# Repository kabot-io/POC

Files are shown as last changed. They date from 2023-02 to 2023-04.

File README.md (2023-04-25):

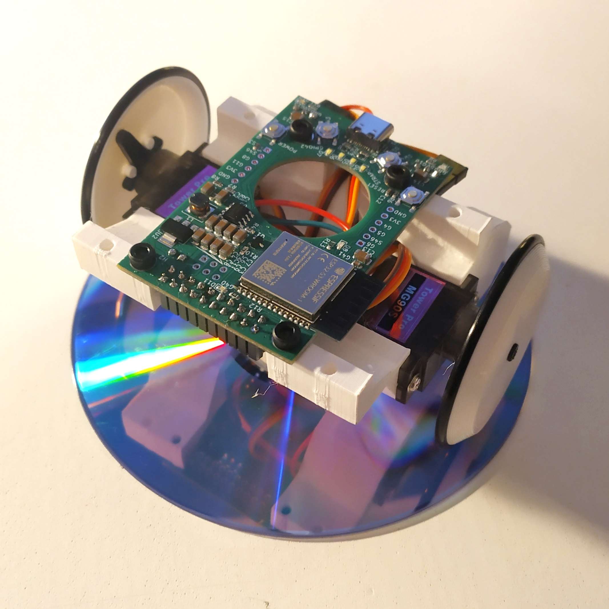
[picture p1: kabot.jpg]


# Kabot - lowering entry barrier to ROS2

The Kabot robot is a hardware and software solution that lowers the entry barrier to Robot Operating System 2 (ROS2) and provides an expandable platform for makers, students and educators. One of the main obstacles in the adoption of ROS2 by beginners is the high knowledge barrier needed to setup and start tinkering - Kabot mission is to bring batteries included in a box. Think of using Arduino instead of setting up whole toolchain and build system.

The robot is a simple differential drive robot with expansion port for connecting external sensors and actuators, and instead of classic internal odometry sensors uses external camera to track itself in the world. Main goals are to create as simple (thus cost effective) hardware, move as much of heavy lifting as possible to the host PC instead of the robot itself and provide user with simple software environment.

## Hardware
All of the structural parts are designed for FDM printing. Wheels, base, cell holder - PLA will do. For the tires, standard O-Ring seals are used, as they are easily available for a cost next to nothing.

Kabot has two actuators - MG90S servos in a continous rotation version. This way, no on-board H-Bridge is needed, just one GPIO per motor and 5V power. Those servos also come with horns that can be used to attach wheels securely. 

All the electrons needed to keep the robot running are supplied via single 18650 Li-Ion cell. Charging, battery protection, and switching on and off is provided via IPS5306 - chinesium powerbank IC. Power for the charger is supplied via USB-C connector. This converter provides 5V for the servos and expansion port, and LDO provides 3.3V for the SoC and expansion port.

The main board is based around ESP32-S3 chip, sporting 16MB of flash and 8MB of RAM. Why ESP32-S3 instead of base ESP32? S3 has built-in USB peripheral, that hosts USB-JTAG and USB-CDC out of the box, so flashing, GDB and Serial.println() works without any external hardware. Furthermore, S3 is a little beefier, and has reconfigurable GPIO matrix, which will ease development of add-on boards. Most of the communication and other internal peripherals can be configured to use any pin of the package. 

## Installation

To run the robots, you need to install ROS2 Foxy. ROS2 is a software framework designed for robotic systems development. It provides a set of libraries and tools to help developers create robust and complex robot applications.

To install ROS2 Foxy, please follow the instructions provided on the official ROS2 website: [ROS2 Foxy installation](https://docs.ros.org/en/foxy/Installation.html)

## How to launch
To launch the package, you need to run the following command:
```
ros2 launch kabot_launcher kabot.launch.py
```

This will launch the package and start the necessary nodes and processes. If you encounter any issues while launching the package, please make sure to check whether you have all the required dependent packages. You can use the ROS2 package manager (rosdep) to automatically install all required dependencies.

## License

[Hardware: Creative Commons Attribution-NonCommercial-ShareAlike 4.0 International License](https://github.com/kabot-io/POC/blob/main/hardware/LICENSE)

[Software: Apache License, Version 2.0](https://github.com/kabot-io/POC/blob/main/src/LICENSE)

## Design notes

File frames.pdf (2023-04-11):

view_frames Result

world

camera

Broadcaster: default_authority Average rate: 10000.0
Buffer length: 0.0
Most recent transform: 0.0 Oldest transform: 0.0

Recorded at time: 1680135584.4556208

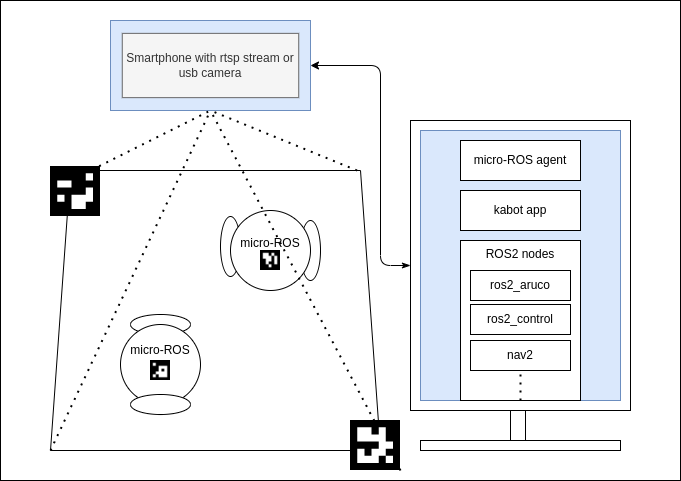
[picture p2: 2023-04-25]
kabot.drawio.png

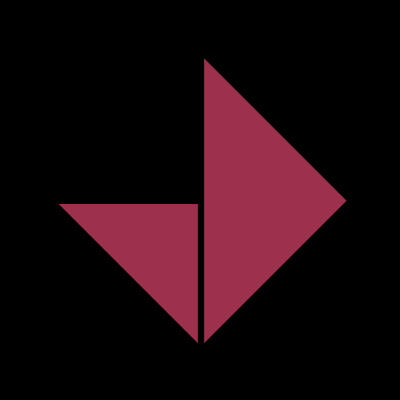
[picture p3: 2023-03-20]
src/kabot_app/src/images/kabot.png

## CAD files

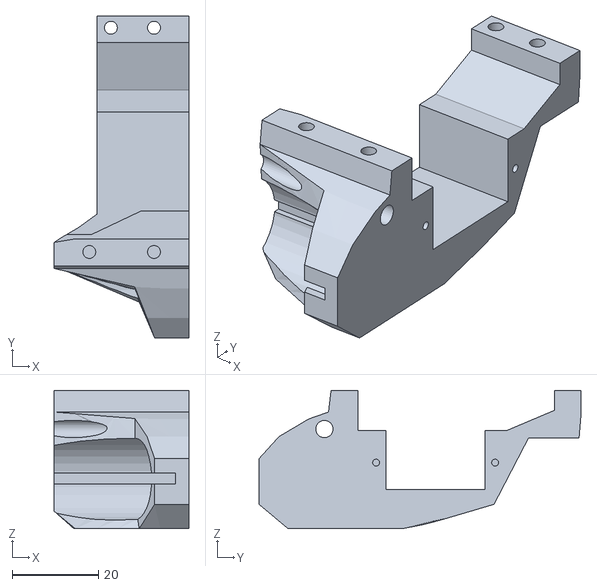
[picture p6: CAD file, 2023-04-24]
hardware/mechanics/printed parts/chassis_right.stl
31.3 x 74.7 x 32.1

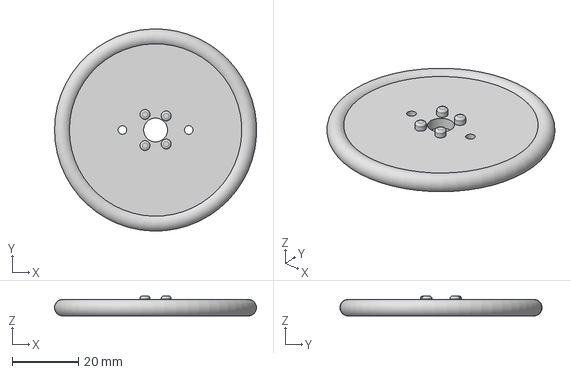
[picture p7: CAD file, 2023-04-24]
hardware/mechanics/printed parts/wheel_v1.step
60.9 x 61.0 x 6.00 mm

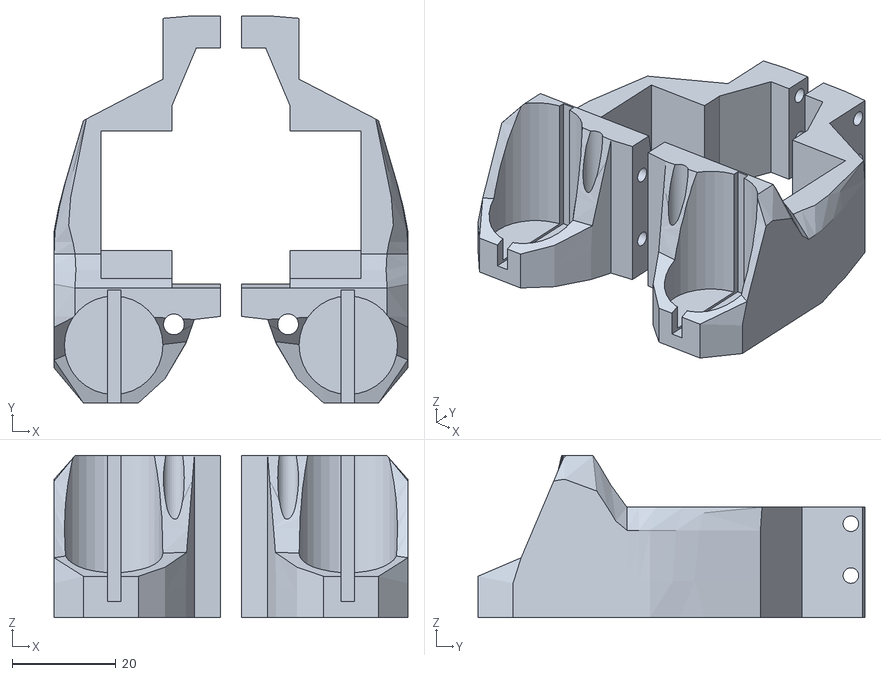
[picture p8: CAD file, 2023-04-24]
hardware/mechanics/printed parts/chassis_both.stl
68.2 x 74.7 x 31.3

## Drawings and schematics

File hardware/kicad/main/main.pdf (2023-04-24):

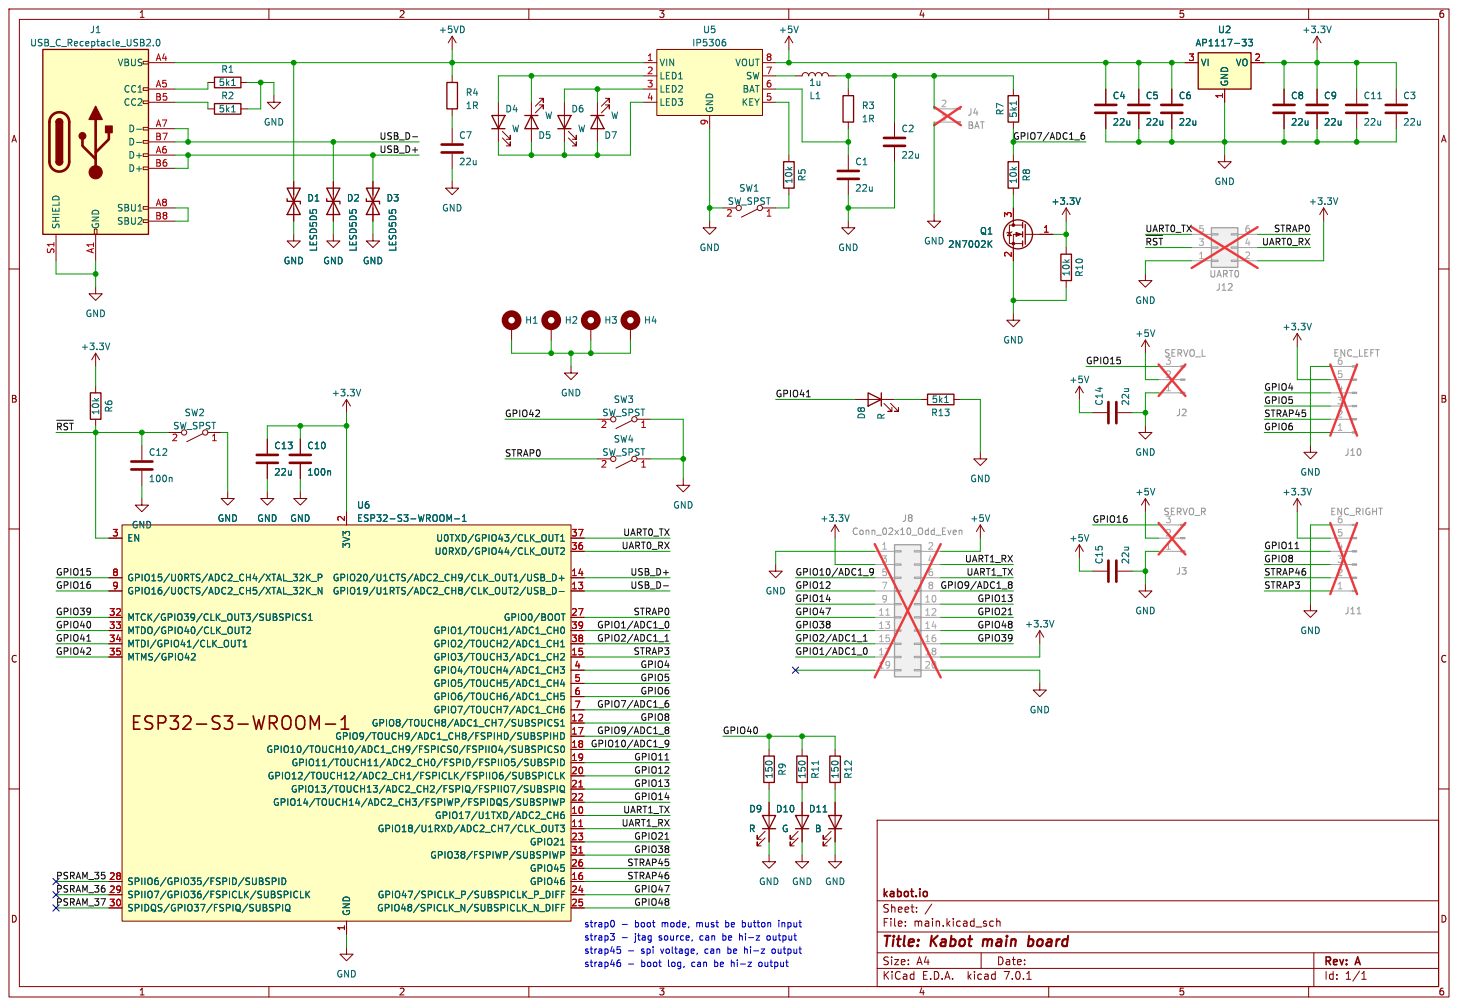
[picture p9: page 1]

2 GPIO12/TOUCH12/ADC2_CH1/FSPICLK/FSPIIO6/SUBSPICLK 20 GPIO13/TOUCH13/ADC2_CH2/FSPIQ/FSPIIO7/SUBSPIQ 21 GPIO14/TOUCH14/ADC2_CH3/FSPIWP/FSPIDQS/SUBSPIWP 22 GPIO21 23 GPIO47/SPICLK_P/SUBSPICLK_P_DIFF 24 GPIO48/SPICLK_N/SUBSPICLK_N_DIFF 25 GPIO45 26 GPIO0/BOOT 27 SPIIO6/GPIO35/FSPID/SUBSPID 28 SPIIO7/GPIO36/FSPICLK/SUBSPICLK 29 EN 3 SPIDQS/GPIO37/FSPIQ/SUBSPIQ 30 GPIO38/FSPIWP/SUBSPIWP 31 MTCK/GPIO39/CLK_OUT3/SUBSPICS1 32 MTDO/GPIO40/CLK_OUT2 33 MTDI/GPIO41/CLK_OUT1 34 MTMS/GPIO42 35 U0RXD/GPIO44/CLK_OUT2 36 U0TXD/GPIO43/CLK_OUT1 37 GPIO2/TOUCH2/ADC1_CH1 38 GPIO1/TOUCH1/ADC1_CH0 39 GPIO4/TOUCH4/ADC1_CH3 4 GPIO5/TOUCH5/ADC1_CH4 5 GPIO6/TOUCH6/ADC1_CH5 6 GPIO7/TOUCH7/ADC1_CH6 7 GPIO15/U0RTS/ADC2_CH4/XTAL_32K_P 8 GPIO16/U0CTS/ADC2_CH5/XTAL_32K_N 9 U6ESP32-S3-WROOM-1 GND

File: main.kicad_sch Sheet: / kabot.io C12

2 GPIO12/TOUCH12/ADC2_CH1/FSPICLK/FSPIIO6/SUBSPICLK 20 GPIO13/TOUCH13/ADC2_CH2/FSPIQ/FSPIIO7/SUBSPIQ 21 GPIO14/TOUCH14/ADC2_CH3/FSPIWP/FSPIDQS/SUBSPIWP 22 GPIO21 23 GPIO47/SPICLK_P/SUBSPICLK_P_DIFF 24 GPIO48/SPICLK_N/SUBSPICLK_N_DIFF 25 GPIO45 26 GPIO0/BOOT 27 SPIIO6/GPIO35/FSPID/SUBSPID 28 SPIIO7/GPIO36/FSPICLK/SUBSPICLK 29 EN 3 SPIDQS/GPIO37/FSPIQ/SUBSPIQ 30 GPIO38/FSPIWP/SUBSPIWP 31 MTCK/GPIO39/CLK_OUT3/SUBSPICS1 32 MTDO/GPIO40/CLK_OUT2 33 MTDI/GPIO41/CLK_OUT1 34 MTMS/GPIO42 35 U0RXD/GPIO44/CLK_OUT2 36 U0TXD/GPIO43/CLK_OUT1 37 GPIO2/TOUCH2/ADC1_CH1 38 GPIO1/TOUCH1/ADC1_CH0 39 GPIO4/TOUCH4/ADC1_CH3 4 GPIO5/TOUCH5/ADC1_CH4 5 GPIO6/TOUCH6/ADC1_CH5 6 GPIO7/TOUCH7/ADC1_CH6 7 GPIO15/U0RTS/ADC2_CH4/XTAL_32K_P 8 GPIO16/U0CTS/ADC2_CH5/XTAL_32K_N 9 D10G
D11B D9 R GND

1 GPIO17/U1TXD/ADC2_CH6 10 GPIO18/U1RXD/ADC2_CH7/CLK_OUT3 11 GPIO8/TOUCH8/ADC1_CH7/SUBSPICS1 12 GPIO19/U1RTS/ADC2_CH8/CLK_OUT2/USB_D- 13 GPIO20/U1CTS/ADC2_CH9/CLK_OUT1/USB_D+ 14 GPIO3/TOUCH3/ADC1_CH2 15 GPIO46 16 GPIO9/TOUCH9/ADC1_CH8/FSPIHD/SUBSPIHD 17 GPIO10/TOUCH10/ADC1_CH9/FSPICS0/FSPIIO4/SUBSPICS0 18 GPIO11/TOUCH11/ADC2_CH0/FSPID/FSPIIO5/SUBSPID 19 3V3

Id: 1/1 Title: Kabot main board

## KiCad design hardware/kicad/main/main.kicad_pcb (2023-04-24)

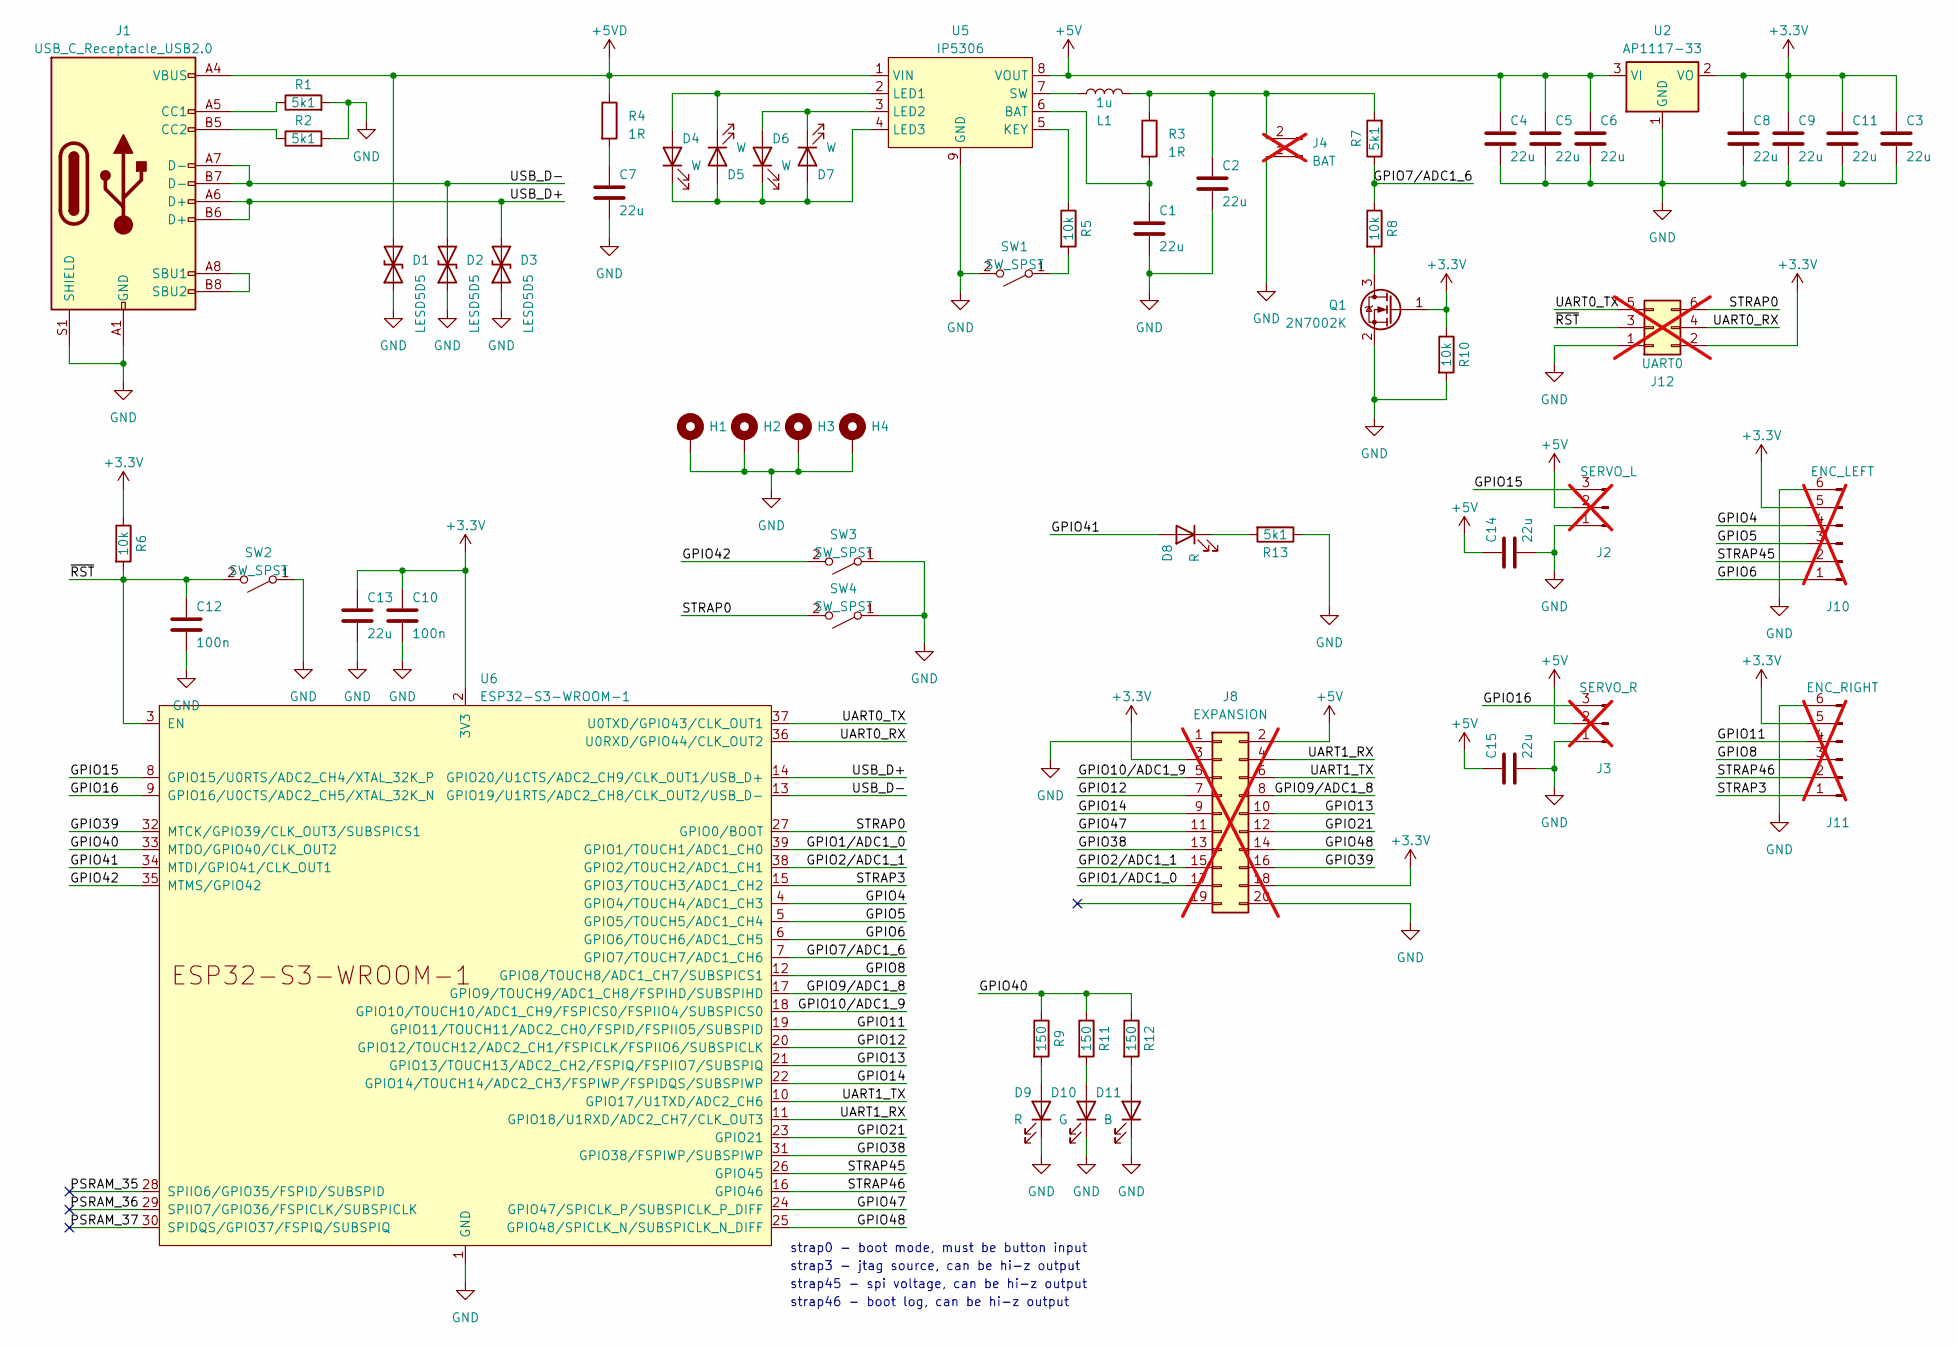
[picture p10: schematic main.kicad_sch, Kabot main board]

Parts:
C1, C2, C3, C4, C5, C6, C7, C8, C9, C11, C13, C14, C15: 22u; C_1206_3216Metric; JLC C12891
C10, C12: 100n; C_0603_1608Metric; JLC C14663
D1, D2, D3: LESD5D5; D_SOD-523; JLC C383211
D4, D5, D6, D7: W; LED_0603_1608Metric; JLC C2290
D8, D9: R; LED_0603_1608Metric; JLC C2286
D10: G; LED_0603_1608Metric; JLC C72043
D11: B; LED_0603_1608Metric; JLC C72041
H1, H2, H3, H4: MountingHole_Pad; MountingHole_3.2mm_M3_DIN965_Pad
J1: USB_C_Receptacle_USB2.0; USB_C_Receptacle_HRO_TYPE-C-31-M-12; JLC C668624
J2: SERVO_L; PinHeader_1x03_P2.54mm_Horizontal; not fitted
J3: SERVO_R; PinHeader_1x03_P2.54mm_Horizontal; not fitted
J4: BAT; PinHeader_1x02_P2.54mm_Horizontal; not fitted
J8: EXPANSION; PinSocket_2x10_P2.54mm_Vertical; JLC C124419; not fitted
J10: ENC_LEFT; PinHeader_1x06_P2.54mm_Horizontal; not fitted
J11: ENC_RIGHT; PinHeader_1x06_P2.54mm_Horizontal; not fitted
J12: UART0; PinHeader_2x03_P2.54mm_Vertical; not fitted
L1: 1u; L_Changjiang_FNR5045S; JLC C436396
Q1: 2N7002K; SOT-23; JLC C8545
R1, R2, R7, R13: 5k1; R_0603_1608Metric; JLC C23186
R3, R4: 1R; R_0603_1608Metric; JLC C22936
R5, R6, R8, R10: 10k; R_0603_1608Metric; JLC C25804
R9, R11, R12: 150; R_0603_1608Metric; JLC C22808
SW1, SW2, SW3, SW4: SW_SPST; SW_SPST_SKQG_WithStem; JLC C318884
U2: AP1117-33; SOT-223-3_TabPin2; JLC C6186
U5: IP5306; Diodes_SO-8EP; JLC C181692
U6: ESP32-S3-WROOM-1; JLC C2913202

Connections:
+3.3V: C3.1, C8.1, C9.1, C10.1, C11.1, C13.1, J8.3, J8.18, J10.5, J11.5, J12.2, Q1.1 (G), R6.1, R10.1, U2.2 (VO), U6.2 (3V3)
+5V: C4.1, C5.1, C6.1, C14.1, C15.1, J2.2, J3.2, J8.2, U2.3 (VI), U5.8 (VOUT)
+5VD: D1.2 (A2), J1.A4 (VBUS), J1.A9 (VBUS), J1.B4 (VBUS), J1.B9 (VBUS), R4.1, U5.1 (VIN)
/GPIO1/ADC1_0: J8.17, U6.39 (GPIO1/TOUCH1/ADC1_CH0)
/GPIO2/ADC1_1: J8.15, U6.38 (GPIO2/TOUCH2/ADC1_CH1)
/GPIO4: J10.4, U6.4 (GPIO4/TOUCH4/ADC1_CH3)
/GPIO5: J10.3, U6.5 (GPIO5/TOUCH5/ADC1_CH4)
/GPIO6: J10.1, U6.6 (GPIO6/TOUCH6/ADC1_CH5)
/GPIO7/ADC1_6: R7.1, R8.1, U6.7 (GPIO7/TOUCH7/ADC1_CH6)
/GPIO8: J11.3, U6.12 (GPIO8/TOUCH8/ADC1_CH7/SUBSPICS1)
/GPIO9/ADC1_8: J8.8, U6.17 (GPIO9/TOUCH9/ADC1_CH8/FSPIHD/SUBSPIHD)
/GPIO10/ADC1_9: J8.5, U6.18 (GPIO10/TOUCH10/ADC1_CH9/FSPICS0/FSPIIO4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)
/GPIO11: J11.4, U6.19 (GPIO11/TOUCH11/ADC2_CH0/FSPID/FSPIIO5/S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)
/GPIO12: J8.7, U6.20 (GPIO12/TOUCH12/ADC2_CH1/FSPICLK/FSPIIO6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)
/GPIO13: J8.10, U6.21 (GPIO13/TOUCH13/ADC2_CH2/FSPIQ/FSPIIO7/S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)
/GPIO14: J8.9, U6.22 (GPIO14/TOUCH14/ADC2_CH3/FSPIWP/FSPIDQS/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)
/GPIO15: J2.3, U6.8 (GPIO15/U0RTS/ADC2_CH4/XTAL_32K_P)
/GPIO16: J3.3, U6.9 (GPIO16/U0CTS/ADC2_CH5/XTAL_32K_N)
/GPIO21: J8.12, U6.23 (GPIO21)
/GPIO38: J8.13, U6.31 (GPIO38/FSPIWP/SUBSPIWP)
/GPIO39: J8.16, U6.32 (MTCK/GPIO39/CLK_OUT3/SUBSPICS1)
/GPIO40: R9.1, R11.1, R12.1, U6.33 (MTDO/GPIO40/CLK_OUT2)
/GPIO41: D8.2 (A), U6.34 (MTDI/GPIO41/CLK_OUT1)
/GPIO42: SW3.2 (B), U6.35 (MTMS/GPIO42)
/GPIO47: J8.11, U6.24 (GPIO47/SPICLK_P/SUBSPICLK_P_DIFF)
/GPIO48: J8.14, U6.25 (GPIO48/SPICLK_N/SUBSPICLK_N_DIFF)
/PSRAM_35: U6.28 (SPIIO6/GPIO35/FSPID/SUBSPID)
/PSRAM_36: U6.29 (SPIIO7/GPIO36/FSPICLK/SUBSPICLK)
/PSRAM_37: U6.30 (SPIDQS/GPIO37/FSPIQ/SUBSPIQ)
/STRAP0: J12.6, SW4.2 (B), U6.27 (GPIO0/BOOT)
/STRAP3: J11.1, U6.15 (GPIO3/TOUCH3/ADC1_CH2)
/STRAP45: J10.2, U6.26 (GPIO45)
/STRAP46: J11.2, U6.16 (GPIO46)
/UART0_RX: J12.4, U6.36 (U0RXD/GPIO44/CLK_OUT2)
/UART0_TX: J12.5, U6.37 (U0TXD/GPIO43/CLK_OUT1)
/UART1_RX: J8.4, U6.11 (GPIO18/U1RXD/ADC2_CH7/CLK_OUT3)
/UART1_TX: J8.6, U6.10 (GPIO17/U1TXD/ADC2_CH6)
/USB_D+: D3.2 (A2), J1.A6 (D+), J1.B6 (D+), U6.14 (GPIO20/U1CTS/ADC2_CH9/CLK_OUT1/USB_D+)
/USB_D-: D2.2 (A2), J1.A7 (D-), J1.B7 (D-), U6.13 (GPIO19/U1RTS/ADC2_CH8/CLK_OUT2/USB_D-)
/~RST: C12.1, J12.3, R6.2, SW2.2 (B), U6.3 (EN)
GND: C1.2, C2.2, C3.2, C4.2, C5.2, C6.2, C7.2, C8.2, C9.2, C10.2, C11.2, C12.2, C13.2, C14.2, C15.2, D1.1 (A1), D2.1 (A1), D3.1 (A1), D9.1 (K), D10.1 (K), D11.1 (K), H1.1, H2.1, H3.1, H4.1, J1.A1 (GND), J1.A12 (GND), J1.B1 (GND), J1.B12 (GND), J1.S1 (SHIELD), J2.1, J3.1, J4.1, J8.1, J8.20, J10.6, J11.6, J12.1, Q1.2 (S), R1.2, R2.2, R10.2, R13.1, SW1.2 (B), SW2.1 (A), SW3.1 (A), SW4.1 (A), U2.1 (GND), U5.9 (GND), U6.1 (GND), U6.40 (GND), U6.41 (GND)
unnamed: C7.1, R4.2
unnamed: D4.2 (A), D5.1 (K), U5.2 (LED1)
unnamed: D4.1 (K), D5.2 (A), D6.1 (K), D7.2 (A), U5.4 (LED3)
unnamed: D6.2 (A), D7.1 (K), U5.3 (LED2)
unnamed: D8.1 (K), R13.2
unnamed: D9.2 (A), R9.2
unnamed: D10.2 (A), R11.2
unnamed: D11.2 (A), R12.2
unnamed: J1.A5 (CC1), R1.1
unnamed: J1.B5 (CC2), R2.1
unnamed: J1.A8 (SBU1), J1.B8 (SBU2)
unnamed: C2.1, J4.2, L1.2, R3.1, R7.2
unnamed: Q1.3 (D), R8.2
unnamed: R5.2, SW1.1 (A)
unnamed: C1.1, R3.2, U5.6 (BAT)
unnamed: R5.1, U5.5 (KEY)
unnamed: L1.1, U5.7 (SW)

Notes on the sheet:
strap3 - jtag source, can be hi-z output
strap45 - spi voltage, can be hi-z output
strap0 - boot mode, must be button input
strap46 - boot log, can be hi-z output

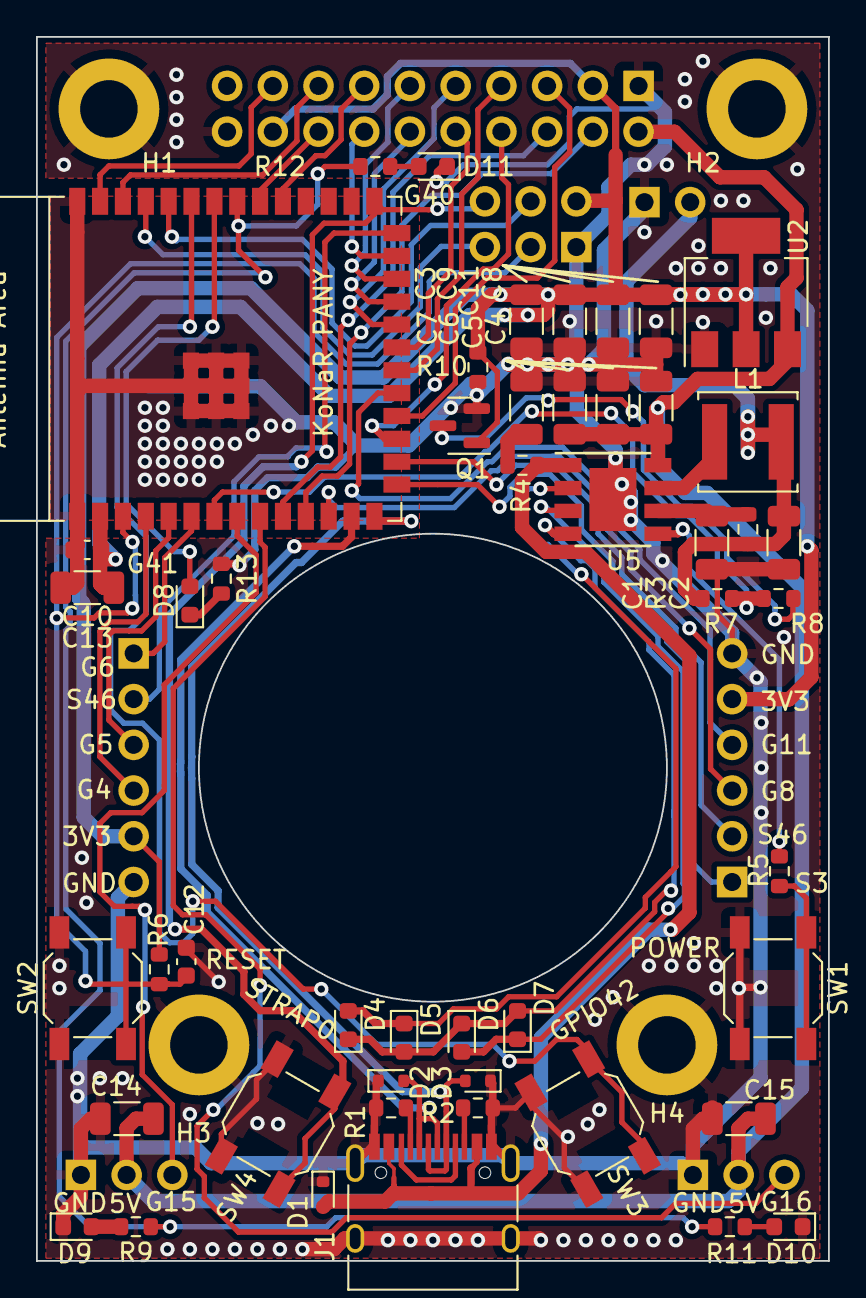
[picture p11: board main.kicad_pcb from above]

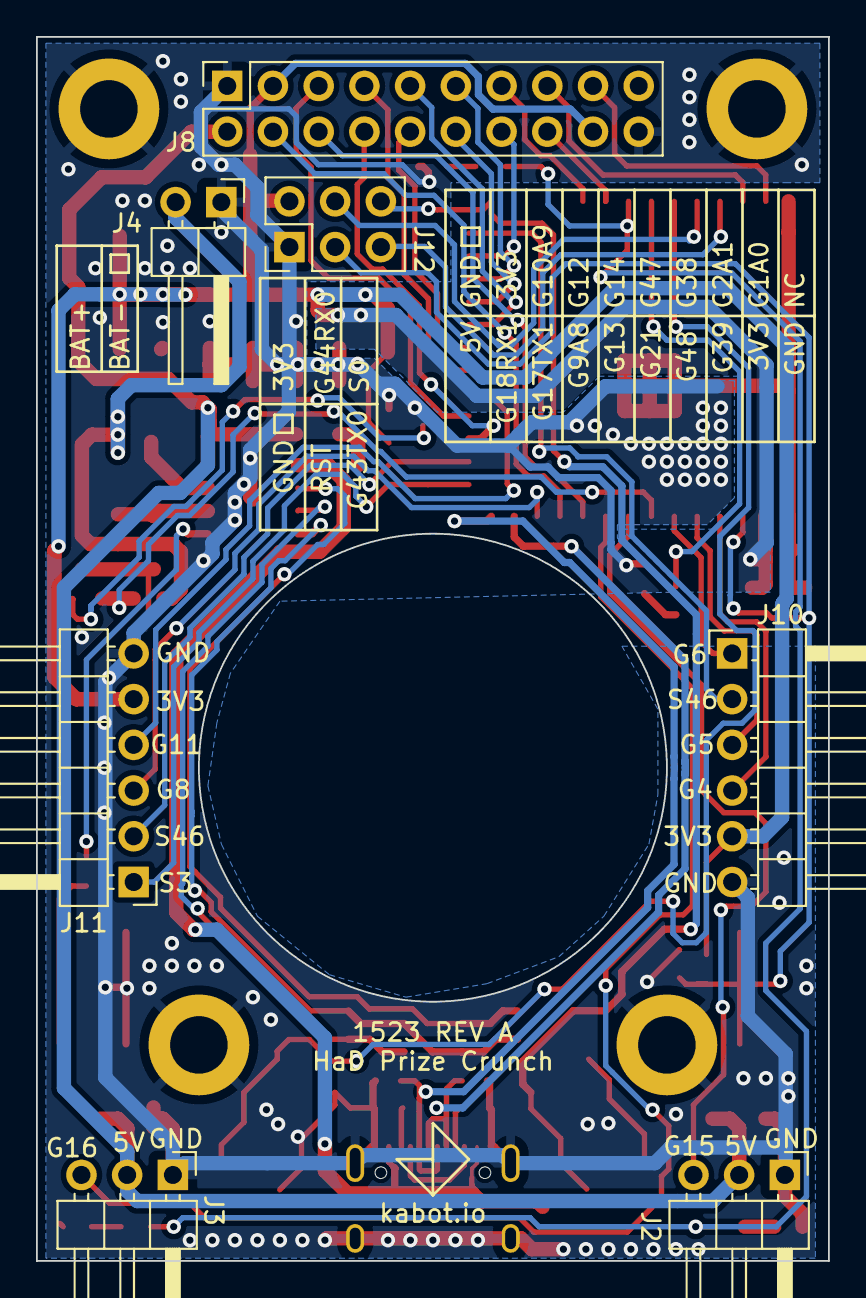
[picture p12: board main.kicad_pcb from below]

Board: 2 copper layers, 44.0 x 68.0 mm, 60 parts (7 on the bottom side), 55 nets.

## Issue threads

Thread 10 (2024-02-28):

🛠️  New mechanical parts

kpochwala, 2024-02-28:
### Description

Create new printed parts. Especially needed is top cover with lightguides for tracking LEDs (short, <5mm stick of transparent filament as optic fiber). Top cover should also have some pushrods to make pressing buttons underneath comfortable.

### DOD

User can print STLs and assemble new version. User can press buttons, and leds are visible from the top.

kpochwala, 2024-02-28:
https://www.thingiverse.com/thing:3469677
https://www.thingiverse.com/thing:3639245
https://pl.aliexpress.com/item/1005003106654416.html

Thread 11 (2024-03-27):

Create some example electronic modules

misiej, 2024-03-27:

misiej, 2024-03-27:
Order min 20 pcs. PCB.
PCB with out  soldering ESP 32.

kpochwala, 2024-03-27:
Ideas:
- see what modules are available for microbit.
- vertical and horizontal perfboard
- cheap sensors board: line sensors, touch (limit switches), some LEDs
- more sophisticated sensors: VL53L0X or similar, microphone, camera?

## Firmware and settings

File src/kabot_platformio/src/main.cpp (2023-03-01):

#include <Arduino.h>
#include <micro_ros_platformio.h>

#include "secrets.h"

#include <rcl/rcl.h>
#include <rcl/error_handling.h>
#include <rclc/rclc.h>
#include <rclc/executor.h>

#include "KabotServo.h"

#if !defined(MICRO_ROS_TRANSPORT_ARDUINO_WIFI)
#error This example is only avaliable for Arduino framework with wifi transport.
#endif

rcl_publisher_t publisher;
rcl_subscription_t subscriber;
geometry_msgs__msg__Twist msg;

rclc_executor_t executor;
rclc_support_t support;
rcl_allocator_t allocator;
rcl_node_t node;

#define RCCHECK(fn) { rcl_ret_t temp_rc = fn; if((temp_rc != RCL_RET_OK)){error_loop();}}
#define RCSOFTCHECK(fn) { rcl_ret_t temp_rc = fn; if((temp_rc != RCL_RET_OK)){}}

// Error handle loop
void error_loop() {
	while(1) {
		delay(100);
	}
}

KabotServo leftServo(0, 500, 2400, 80, ServoSide::Left);
KabotServo rightServo(0, 500, 2400, 80, ServoSide::Right);

void subscription_callback(const void * msgin)
{
	const geometry_msgs__msg__Twist * msg = (const geometry_msgs__msg__Twist *)msgin;
	leftServo.move(msg);
	rightServo.move(msg);
	RCSOFTCHECK(rcl_publish(&publisher, &msg, NULL)); //debug callback
}

void setup() {
	// configure serial transport
	Serial.begin(115200);

	IPAddress agent_ip(192, 168, 1, 187);
	size_t agent_port = 8888;
	set_microros_wifi_transports(ssid, psk, agent_ip, agent_port);

	allocator = rcl_get_default_allocator();

	// create init_options
	RCCHECK(rclc_support_init(&support, 0, NULL, &allocator));

	// create node
	RCCHECK(rclc_node_init_default(&node, "kabot", "", &support));

	// create publisher
	RCCHECK(rclc_publisher_init_default(
		&publisher,
		&node,
		ROSIDL_GET_MSG_TYPE_SUPPORT(geometry_msgs, msg, Twist),
		"/cmd_vel_callback"));

	// create subscriber
	RCCHECK(rclc_subscription_init_default(
		&subscriber,
		&node,
		ROSIDL_GET_MSG_TYPE_SUPPORT(geometry_msgs, msg, Twist),
		"/cmd_vel"));

	// create executor
	RCCHECK(rclc_executor_init(&executor, &support.context, 1, &allocator));
	RCCHECK(rclc_executor_add_subscription(&executor, &subscriber, &msg, &subscription_callback, ON_NEW_DATA));
}

void loop() {
	delay(100);
	RCSOFTCHECK(rclc_executor_spin_some(&executor, RCL_MS_TO_NS(100)));
}

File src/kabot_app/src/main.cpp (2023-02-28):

#include <QGuiApplication>
#include <QQmlApplicationEngine>
#include <QtWidgets/QApplication>

#include "ros2/RosController.h"

int main(int argc, char *argv[])
{
    rclcpp::init(argc, argv);

#if QT_VERSION < QT_VERSION_CHECK(6, 0, 0)
    QCoreApplication::setAttribute(Qt::AA_EnableHighDpiScaling);
#endif
    QApplication::setAttribute(Qt::AA_ShareOpenGLContexts, true);
    QApplication app(argc, argv);
    QQmlApplicationEngine engine;

    QObject::connect(&engine, &QQmlEngine::warnings, [](const QList<QQmlError> &warnings){
        for(auto& warning : warnings){
            logger::warning("QML", warning.toString());
        }
    });

    const QUrl url(QStringLiteral("qrc:/main.qml"));
    QObject::connect(&engine, &QQmlApplicationEngine::objectCreated,
                     &app, [url](QObject *obj, const QUrl &objUrl) {
        if (!obj && url == objUrl)
            QCoreApplication::exit(-1);
    }, Qt::QueuedConnection);

    engine.addImportPath("qrc:/");
    engine.addImportPath("qrc:/qml");

    engine.load(url);

    return app.exec();
}

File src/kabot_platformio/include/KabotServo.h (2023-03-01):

#pragma once

#include <Arduino.h>
#include <micro_ros_platformio.h>
#include <ESP32_Servo.h>

#include <geometry_msgs/msg/twist.h>

enum ServoSide{
	Left,
	Right
};

struct KabotServo{
	KabotServo(int pin, int min, int max, int servoOrigin, ServoSide side){
		m_servo.attach(pin, min, max);
		m_servoOrigin = servoOrigin;
		m_servoLeftRange = servoOrigin;
		m_servoRightRange =  180-servoOrigin;
	}

	void move(const geometry_msgs__msg__Twist *msg){
		int servoVelocity;
		if(m_side == ServoSide::Left){
			servoVelocity = msg->linear.x + msg->angular.z;
        }
        else{
			servoVelocity = msg->linear.x - msg->angular.z;
            servoVelocity *= -1;
        }

        if(servoVelocity > 0){
            servoVelocity = map(servoVelocity, m_minServoVelocity, m_minServoVelocity, m_servoOrigin, m_servoRightRange);
        }
        else{
            servoVelocity = map(servoVelocity, m_minServoVelocity, m_maxServoVelocity, m_servoLeftRange, m_servoOrigin);
        }

		m_servo.write(servoVelocity);
	}

private:
	Servo m_servo;
	ServoSide m_side;

	int m_servoOrigin;
	int m_servoLeftRange;
	int m_servoRightRange;

	const int m_minServoVelocity = -100;
	const int m_maxServoVelocity = 100;
};

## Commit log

2023-03-08 initial hardware dump
    [main.kicad_pcb, main.kicad_sch]
2023-03-09 added battery charging ic, mounting holes
    [main.kicad_pcb, main.kicad_sch]
2023-03-09 fixed paths to be relative, added kicad gitignore, removed auto backups
    [main.kicad_pcb, main.kicad_sch]
2023-03-09 added model of wheel
    [wheel_v1.step]
2023-03-10 used espressif library
    [main.kicad_pcb, main.kicad_sch]
2023-03-22 Aruco detection. Usb camera config files. Improved kabot.launch
2023-03-22 Camera config files, default rviz2 launch
2023-04-11 URDF, improved launcher script
    [chassis.xacro, kabot.urdf.xacro, materials.xacro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]
2023-04-12 most of the routing done, left power supplies and navigation leds
    [main.kicad_pcb, main.kicad_sch]
2023-04-12 Added inertial macros for wheels and chassis
    [chassis.xacro, inertial_macros.xacro, wheel.xacro]
2023-04-12 routing pretty much done, passing DRC
    [main.kicad_pcb, main.kicad_sch]
2023-04-13 Gazebo diff_drive_controller
    [chassis.xacro, kabot.urdf.xacro, wheel.xacro]
2023-04-14 changed buttons to basic ones, fixed inductor footprint, added JLCPCB part numbers to each mounted component for assembly
    [main.kicad_pcb, main.kicad_sch]
2023-04-14 minor dimensions adjustments
    [main.kicad_pcb]
2023-04-14 removed addressable led as it is not really available, fixed inductor footprint, added production files
    [main.kicad_pcb, main.kicad_sch]
2023-04-17 fixed inductor model, added some drawings and dimensions
    [main.kicad_pcb]
2023-04-17 added blend files and stl of chassis
    [chassis_both.stl, chassis_right.stl]
2023-04-18 added interactive bom, updated blend files with more clearance on 18650 cell
    [chassis_both.stl, chassis_right.stl, main.kicad_pcb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]
2023-04-18 moved bom to docs to enable github pages
2023-04-24 First small readme, additional launch files
    [gazebo_camera.urdf.xacro, gazebo_control.xacro, wheel.xacro]
